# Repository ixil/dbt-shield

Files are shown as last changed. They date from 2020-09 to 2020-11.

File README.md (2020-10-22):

# dbt-shield
Shield: Pellet extrusion controller for ABB robotic arms w/ profinet I/O

Mini-shield: Filament extrusion controller for UR arms, to be used in the MAS ETH DFAB

## Shield
---
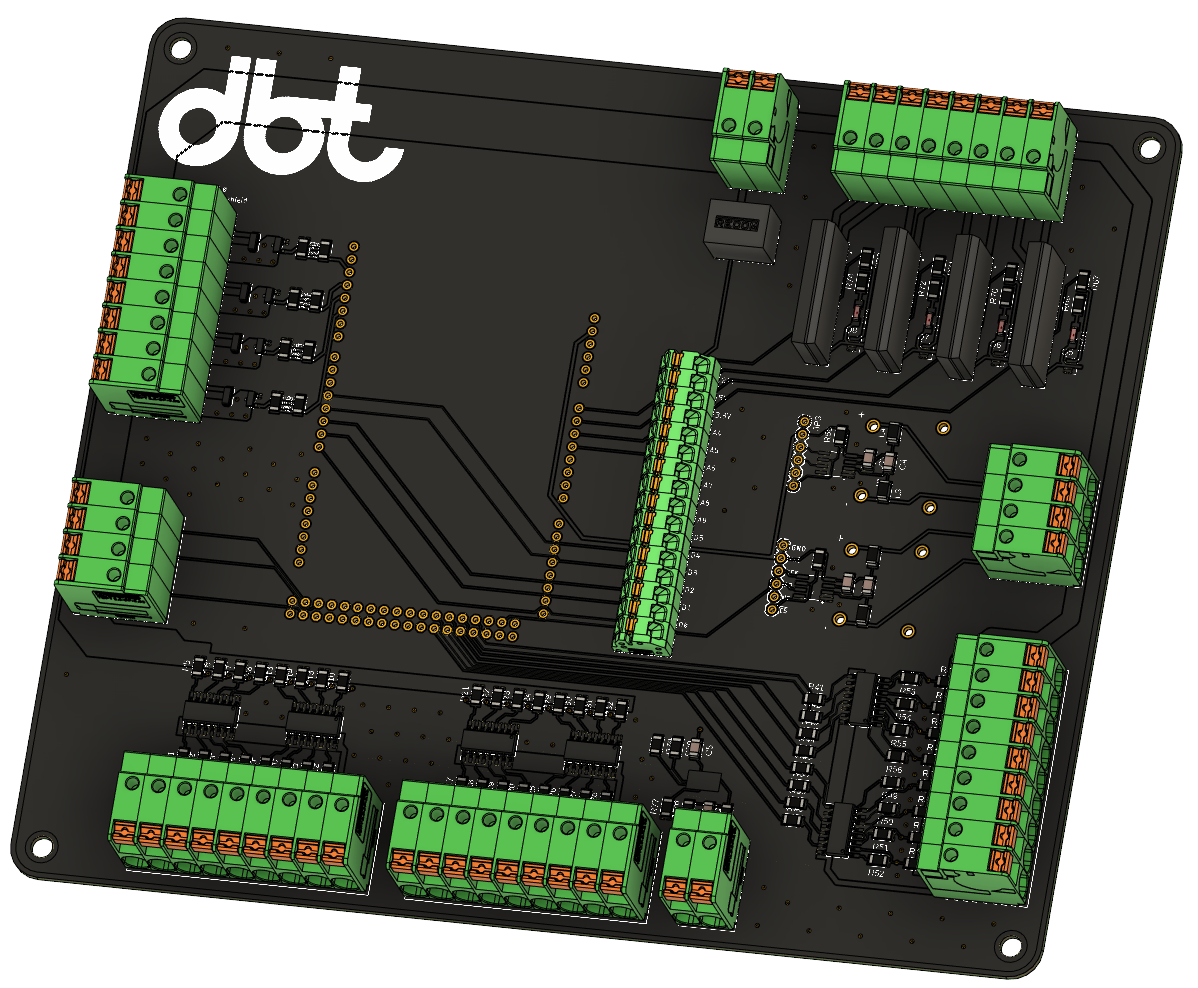
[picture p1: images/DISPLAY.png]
d


### Specs
---
16bit 24V digital Input\
8bit 24v digital Output\
4bit 0-10v analog Input\
4x 500mW MOSFETS\
4x SSR 240VAC 2A\
2x K-Type Thermocouple amplifiers

## Mini-Shield
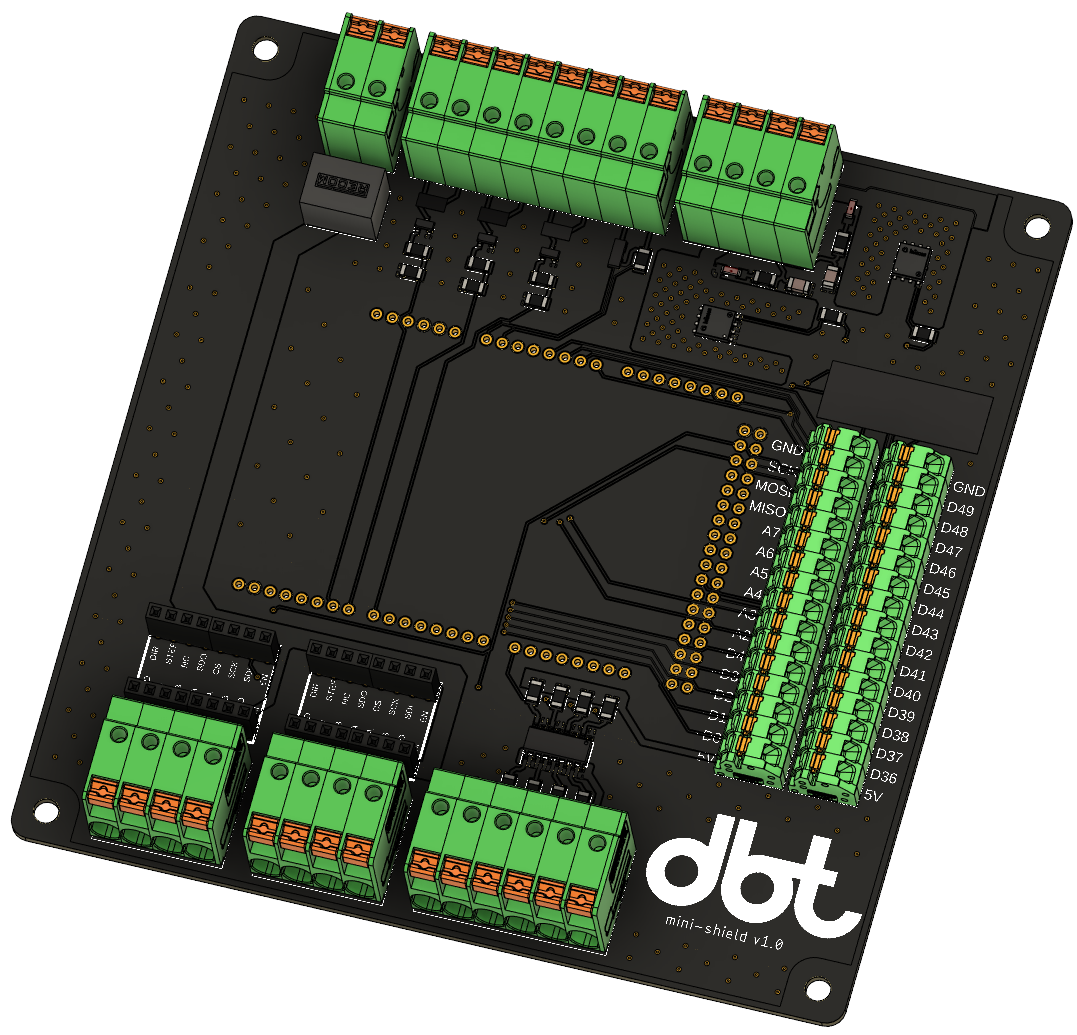
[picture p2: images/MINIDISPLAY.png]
minid


### Specs
---
4bit 24V digital Input\
2x TMC2130 Stepper Driver\
2x 100W MOSFETS\
3x 500mW MOSFETS\
1x 104NT thermistor

[Pin-Out / Set-Up / Connections](https://github.com/hiiragii/dbt-shield/tree/master/mini)

### UR5 FDM  

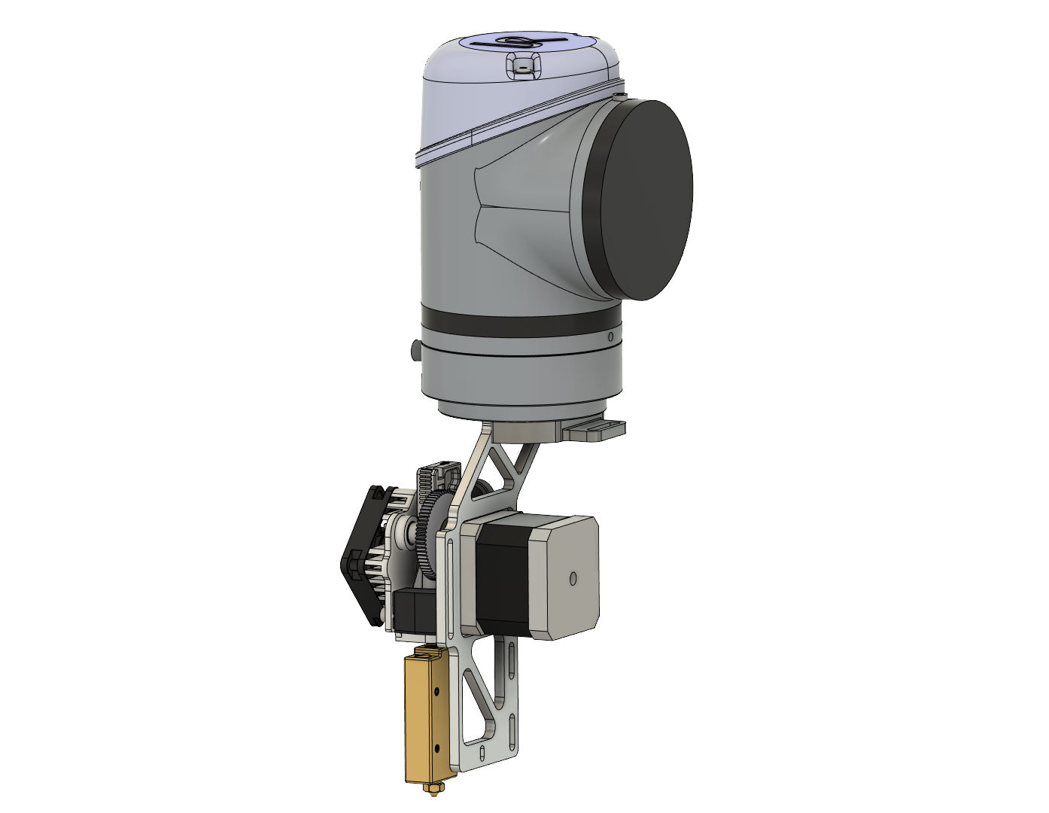
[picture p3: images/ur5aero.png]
ur5


UR 5 e3d Titan Aero + Super Volcano mounting bracket
[stl / step files](https://github.com/hiiragii/dbt-shield/tree/master/ur5aero)

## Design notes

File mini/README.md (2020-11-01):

## Pinout
---
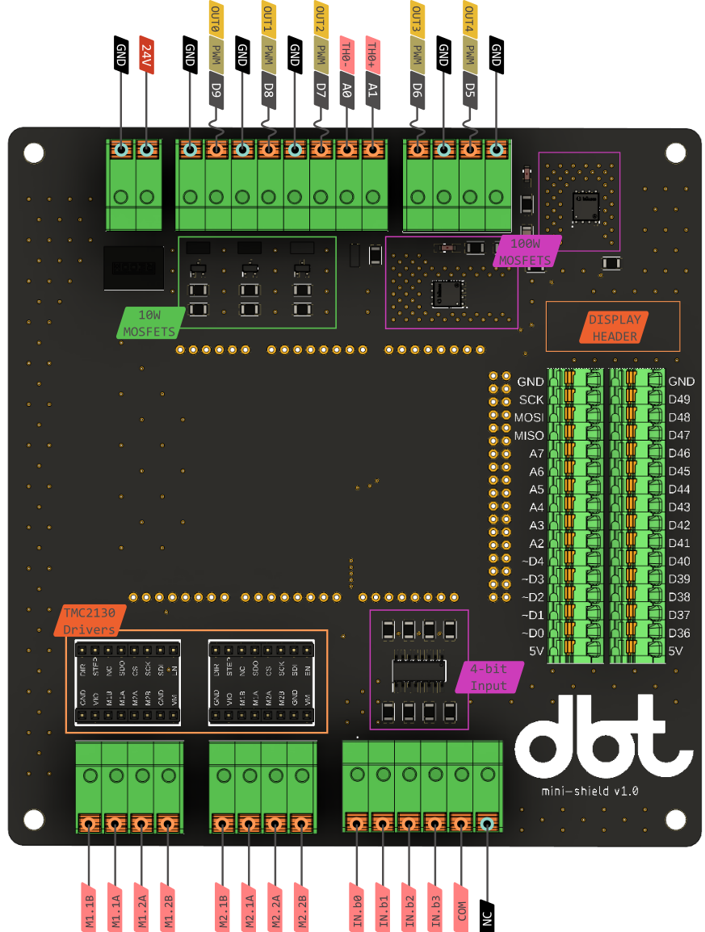
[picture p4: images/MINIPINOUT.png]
pinout

The 2x16 pin terminal blocks on the right side are directly connected to the respective arduino pin (eg D0 on the terminal block is digital pin 0 on the arduino).

## Connections
---
+ Connect the 24v power supply wires to the top terminal.
+ Connect the Extruder optional object fan to OUT0 and OUT1.
+ Connect the thermistor leads to TH0+ and TH0-, polarity doesn't matter.
+ Connect the super-volcano heater to OUT3 and GND (first 2 pins on the terminal block).
+ Connect the first stepper coil to M1.1A and M1.1B. Connect the second coil to M1.2A and M1.2B. Polarity doesn't matter, you can reverse the direction of rotation directly in software or by swapping 2 leads of the same coil (eg. M1.1A and M1.1B).  
+ Connect the 5 lead cable to the 4-bit input terminal block, where IN.b3 is the MSB.

## Set-up
---

## Digital-Input

In.b0 = heater enable, active LOW
In.b1 = stepper enable, active LOW
In.b2 = speed 
In.b3 = speed 

speed(5mm/s)  01
speed(15mm/s) 10
speed(30mm/s) 11

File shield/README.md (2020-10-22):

## Pinout
---
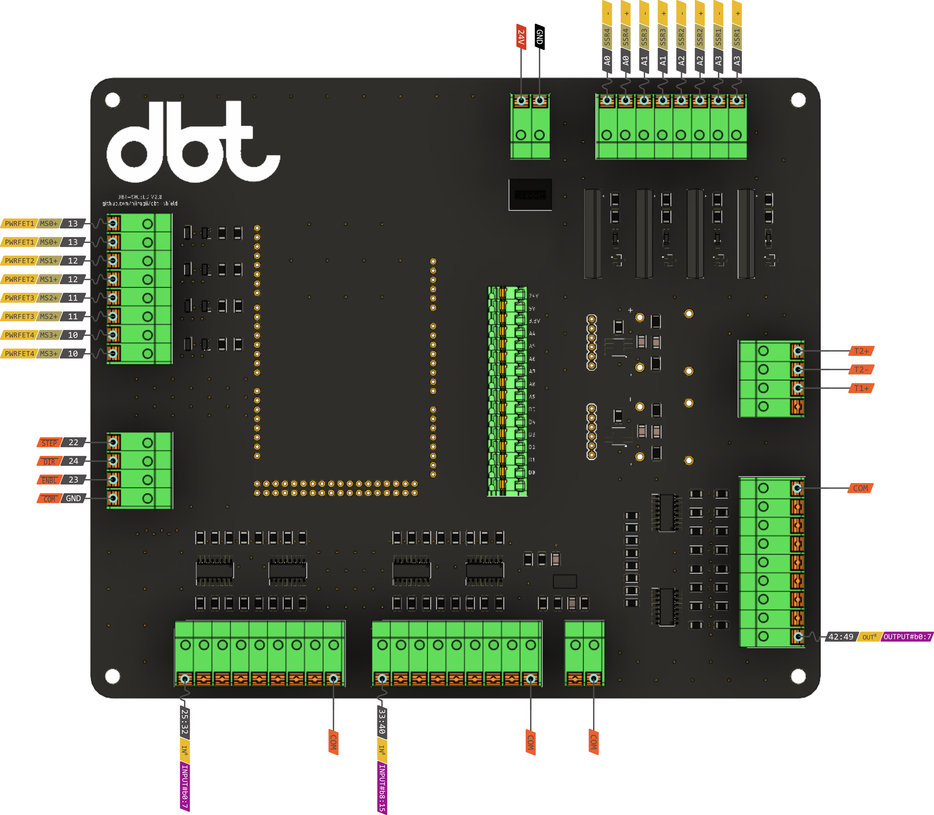
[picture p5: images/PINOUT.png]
pinout


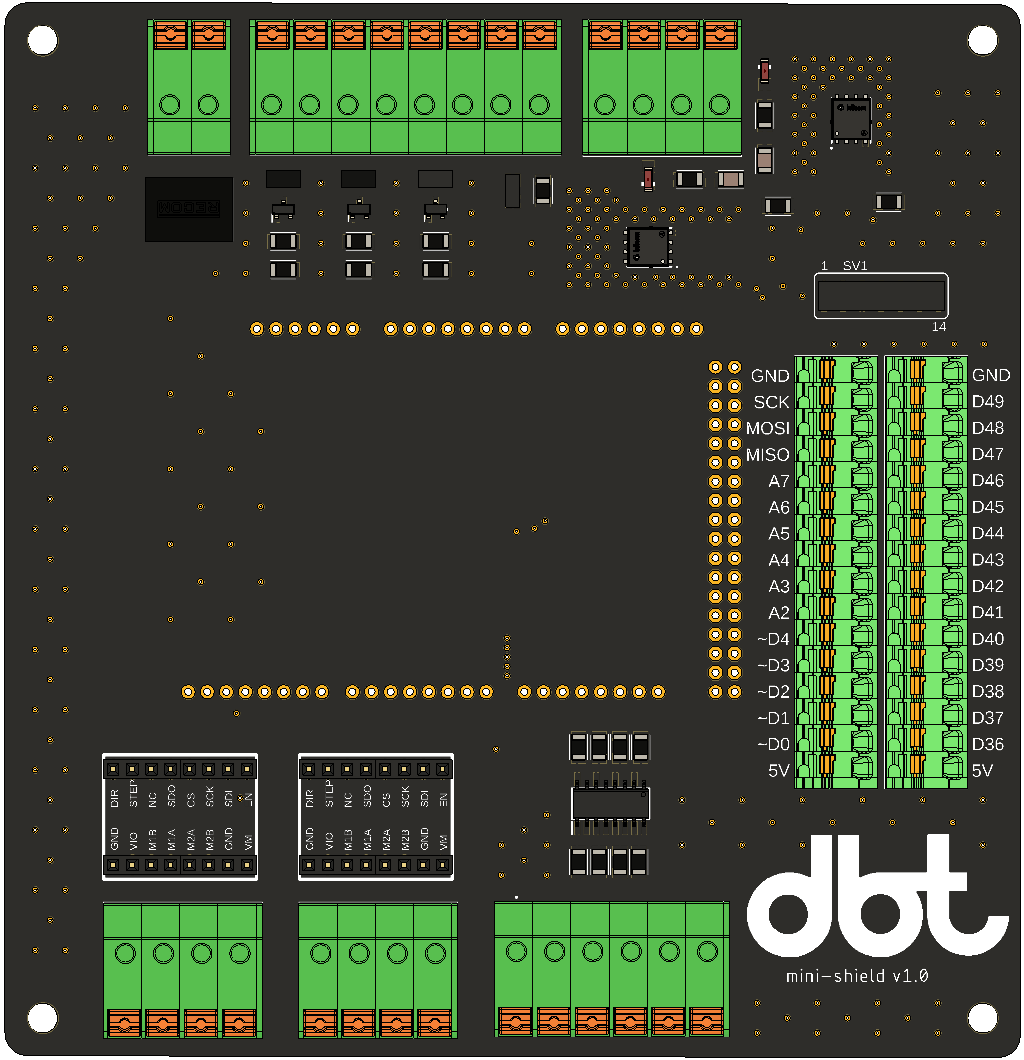
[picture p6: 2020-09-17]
images/MINIFRONT.png

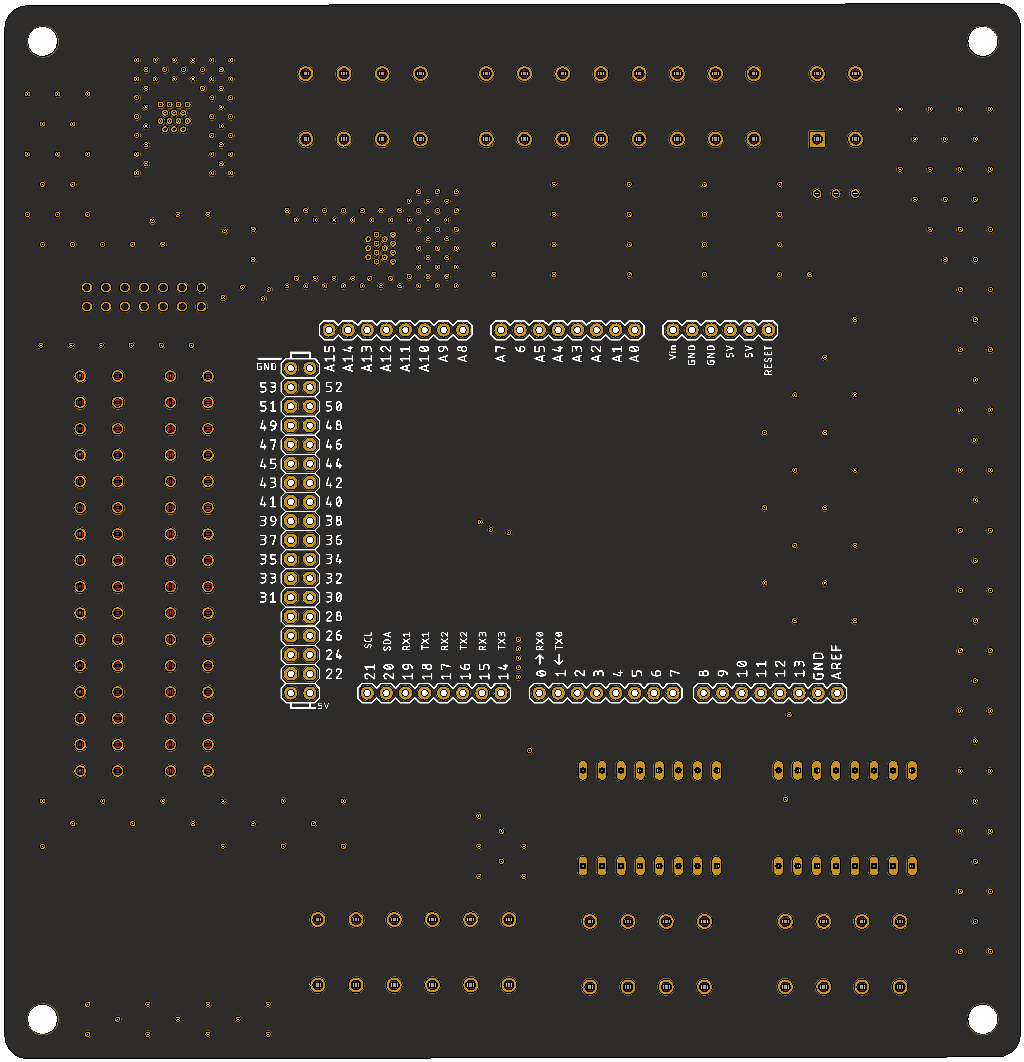
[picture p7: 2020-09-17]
images/MINIBACK.png

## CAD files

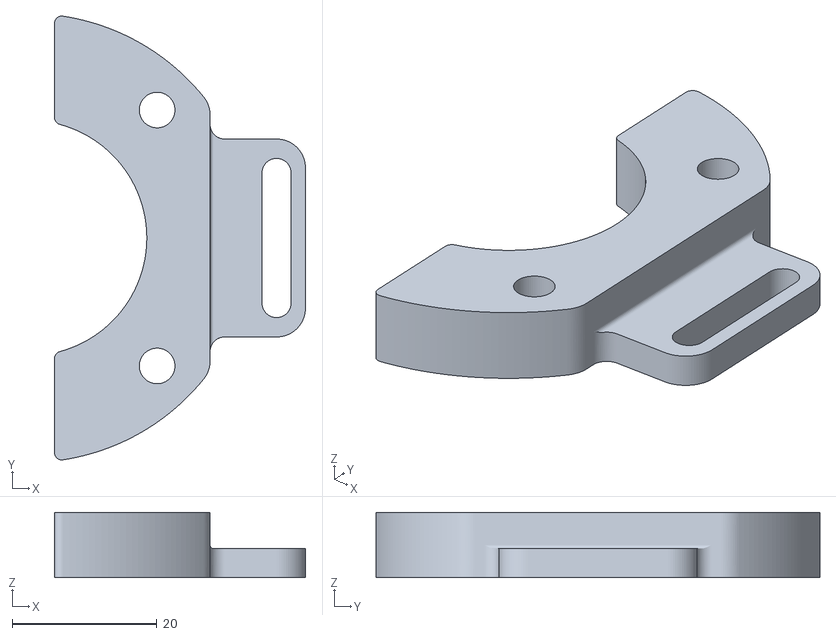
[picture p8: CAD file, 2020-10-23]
ur5aero/dbt-aero-bracket1.stl
34.7 x 61.3 x 9.00

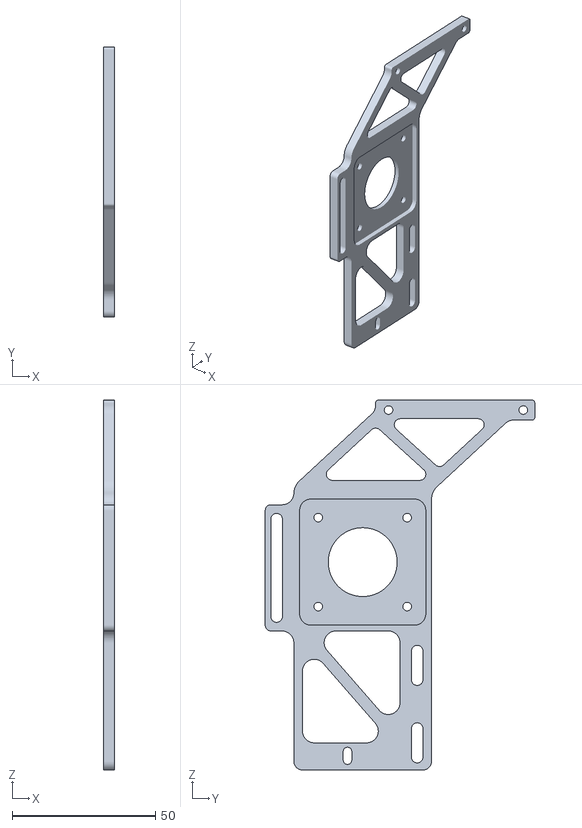
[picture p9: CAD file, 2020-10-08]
ur5aero/dbt_ur5_aero_bracket1.stl
4.00 x 94.0 x 129.0

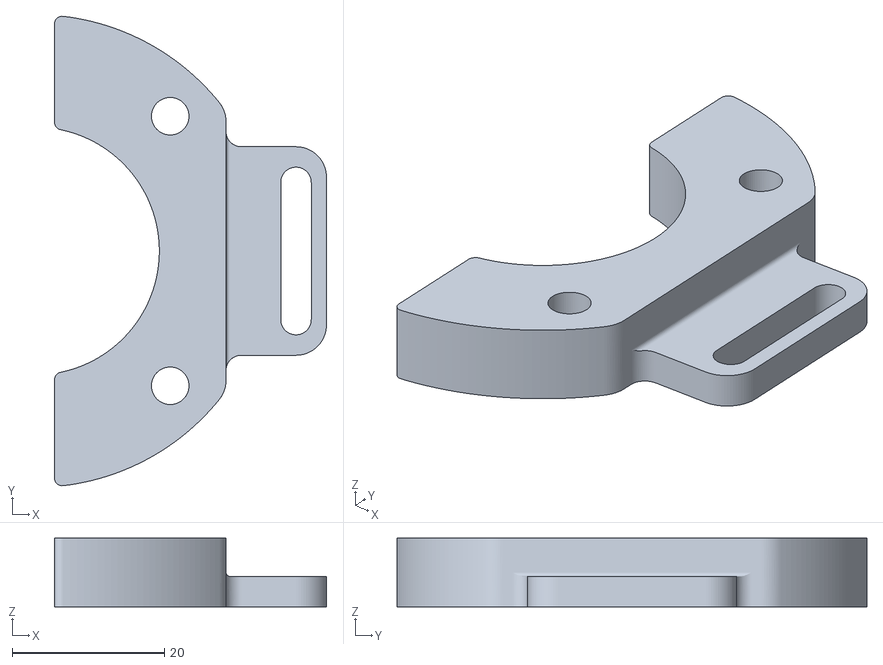
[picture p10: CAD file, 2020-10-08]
ur5aero/dbt_ur5_aero_bracket2.stl
35.7 x 61.6 x 9.00

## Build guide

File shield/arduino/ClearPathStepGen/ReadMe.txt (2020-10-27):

This Library sends pulsed step and Direction signals to ClearPath motors to precisly control position, and velocity of up to 6 motors simulateously up to 4000RPM.  The methodology used to create the pulse step and direction signals is not compatible with stepper motors, or with other servo systems.  The pulsed step and direction also requires a RAS setting of at least 16 ms on all ClearPath motors, a longer RAS will results in quieter motion.

This library defines two classes used to manage and control the motors:ClearPathMotorSD, and ClearPathStepGen.

The ClearPathMotorSD class is used to manage an individual motor including setting up pins, commanding moves, setting velocity/acceleration etc.  The following is a list of commands in this class:

--- ClearPathMotorSD - default constructor for initializing the motor

--- attach() - Attachs pins to this motor, and declares them as input/outputs

--- stopMove()  - Interupts the current move, the motor may abruptly stop

--- move() - sets the maximum veloctiy

--- moveWithVelocity() - moves continuously at a velocity

--- disable() - disables the motor

--- enable() - enables the motor

--- getCommandedPosition() - Returns the absolute cmomanded position where the position on enable=0

--- readHLFB() - Returns the value of the motor's HLFB Pin

--- setMaxVel() - sets the maximum veloctiy

--- setMaxAccel() - sets the acceleration

--- commandDone() - returns wheter or not there is a valid current command

The ClearPathStepGen class is the class which manages the sending of the pulsed step and direction signals to all motors.  This is accomplished by setting up a Timer based ISR at around 2kHz (using Timer2), and directly writing to the I/O register Port B.  Becuase only PORTB is used to send step signals, the B input of the ClearPath motors must be connected to pins 8-13 on an Arduino Uno.  Unused pins on PORTB may be used for other function without interfereing with this library.

NOTE: If you are using another type of arduino besides the UNO, the ClearPathStepGen must be modified to output on a different PORT and/or the Contrustor function must be modified to correctly relate the pin numbers to the bits of the I/O Resister you would like to use.  For example,

In an Arduino Mega, PORTA refers to pins, 22-29, so to modify this library to use a Mega simply:

1) Do a find/replace all replacing "PORTB" with "PORTA"  (case sensitive, ignore quotes).

2) Do a find/replace all replacing "->PinB-8" with "->PinB-22" (case sensitive, ignore quotes).

After this, you could use an Arduino Mega and connect input B to pins 22-29

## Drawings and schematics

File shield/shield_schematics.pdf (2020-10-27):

# ARDUINO / CONNS

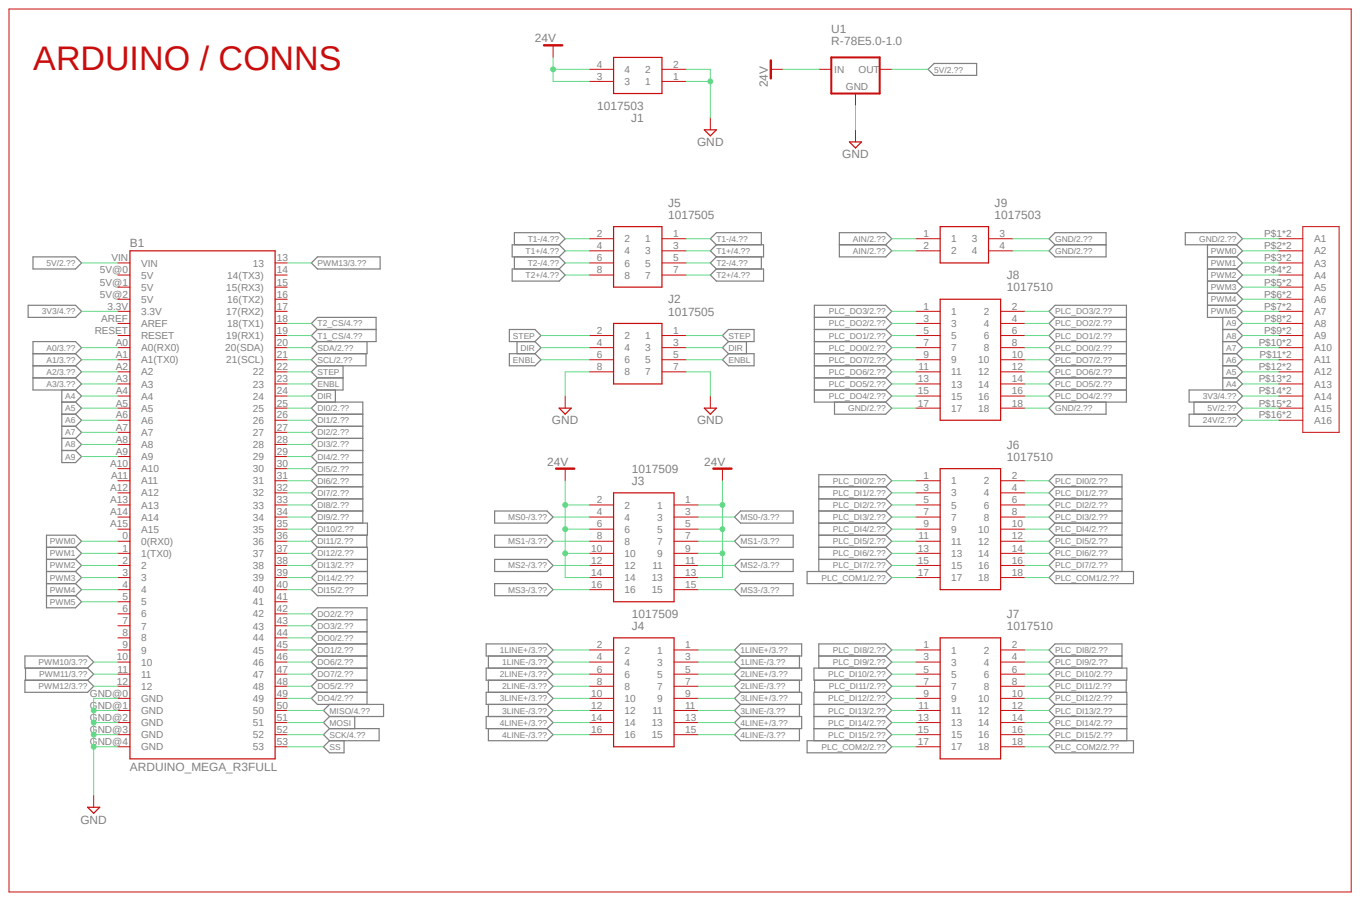
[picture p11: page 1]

MISO/4.?? MOSI SCK/4.?? SS

16-bit Input | 8-bit Output

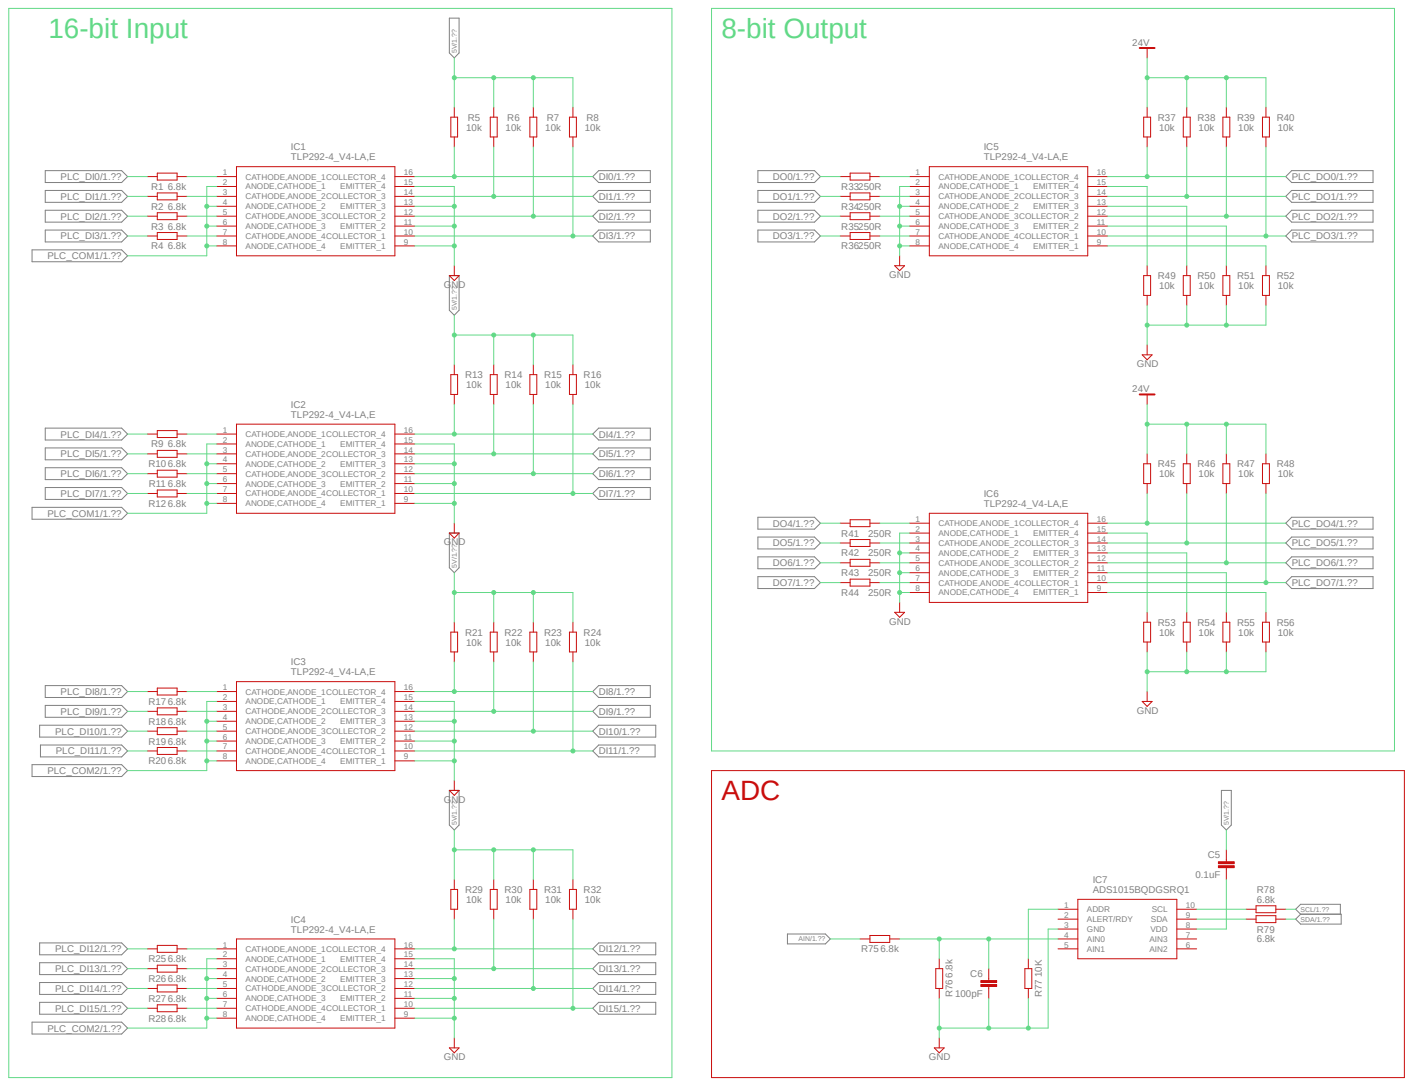
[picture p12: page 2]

24V 10k

24V 10k

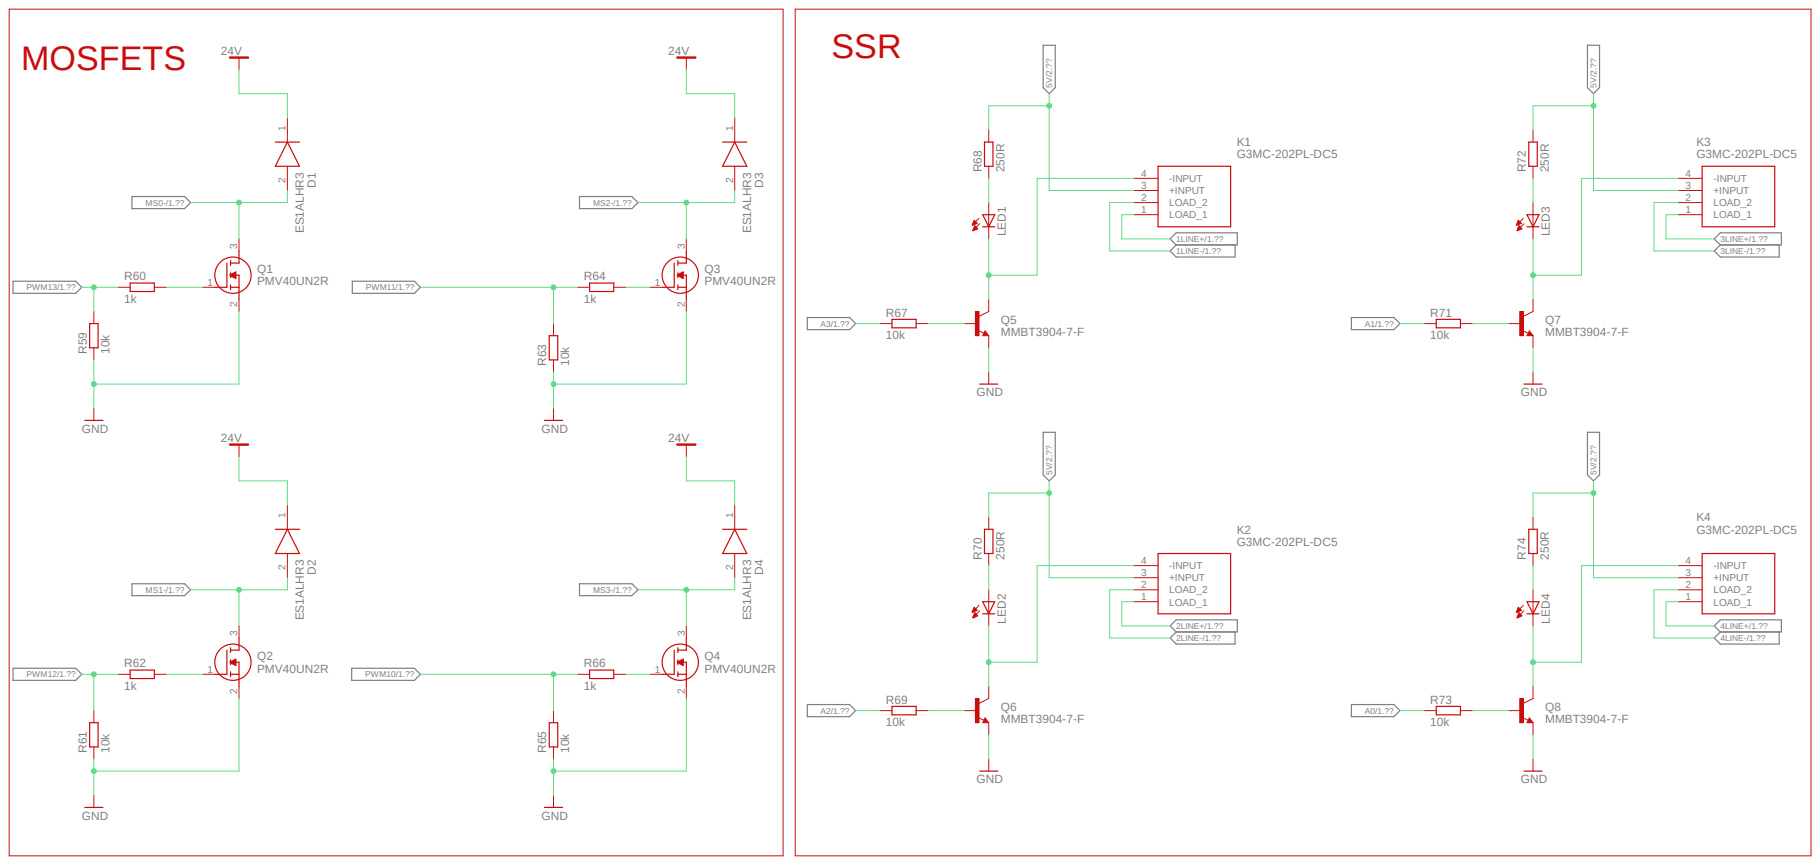
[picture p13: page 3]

# MAX31855K

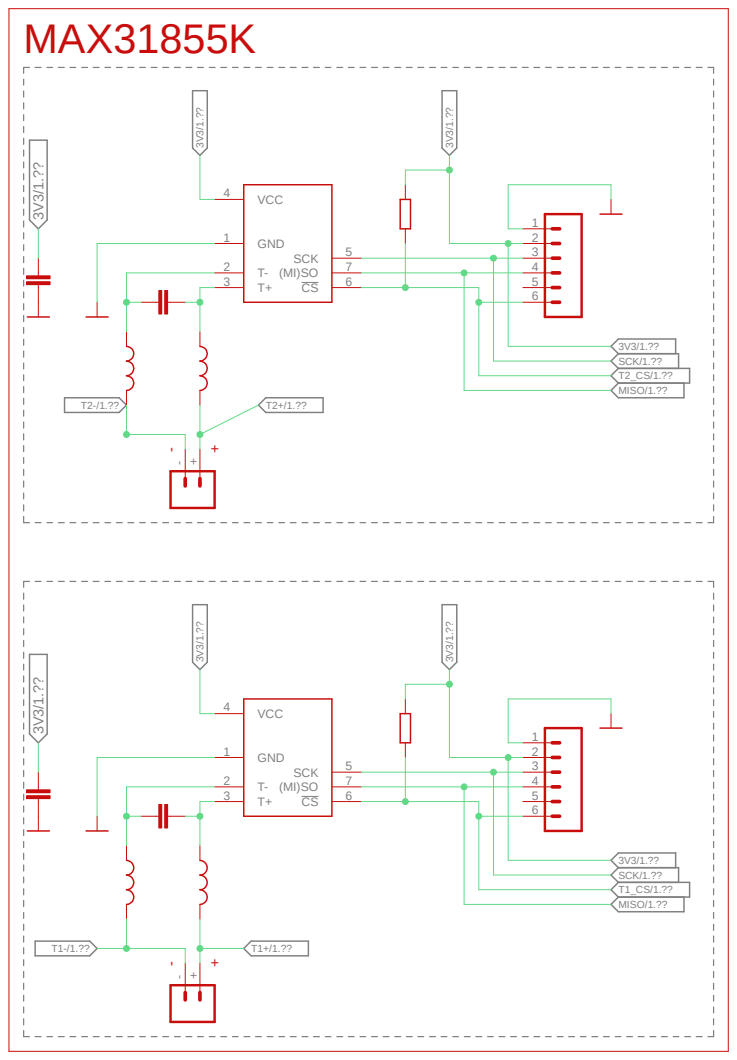
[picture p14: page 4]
GND 1; VCC 4; 6 SCK; -+ GND 1 T- 2 T+ 3 VCC 4; SCK/1.??; T1+/1.?? ³V³/1.??; 3V3/1.?? ³V³/1.??; MISO/1.??; MISO/1.?? T2-/1.??

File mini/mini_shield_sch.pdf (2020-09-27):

# DBT MINI-SHIELD https://github.com/hiiragii/dbt-shield/mini

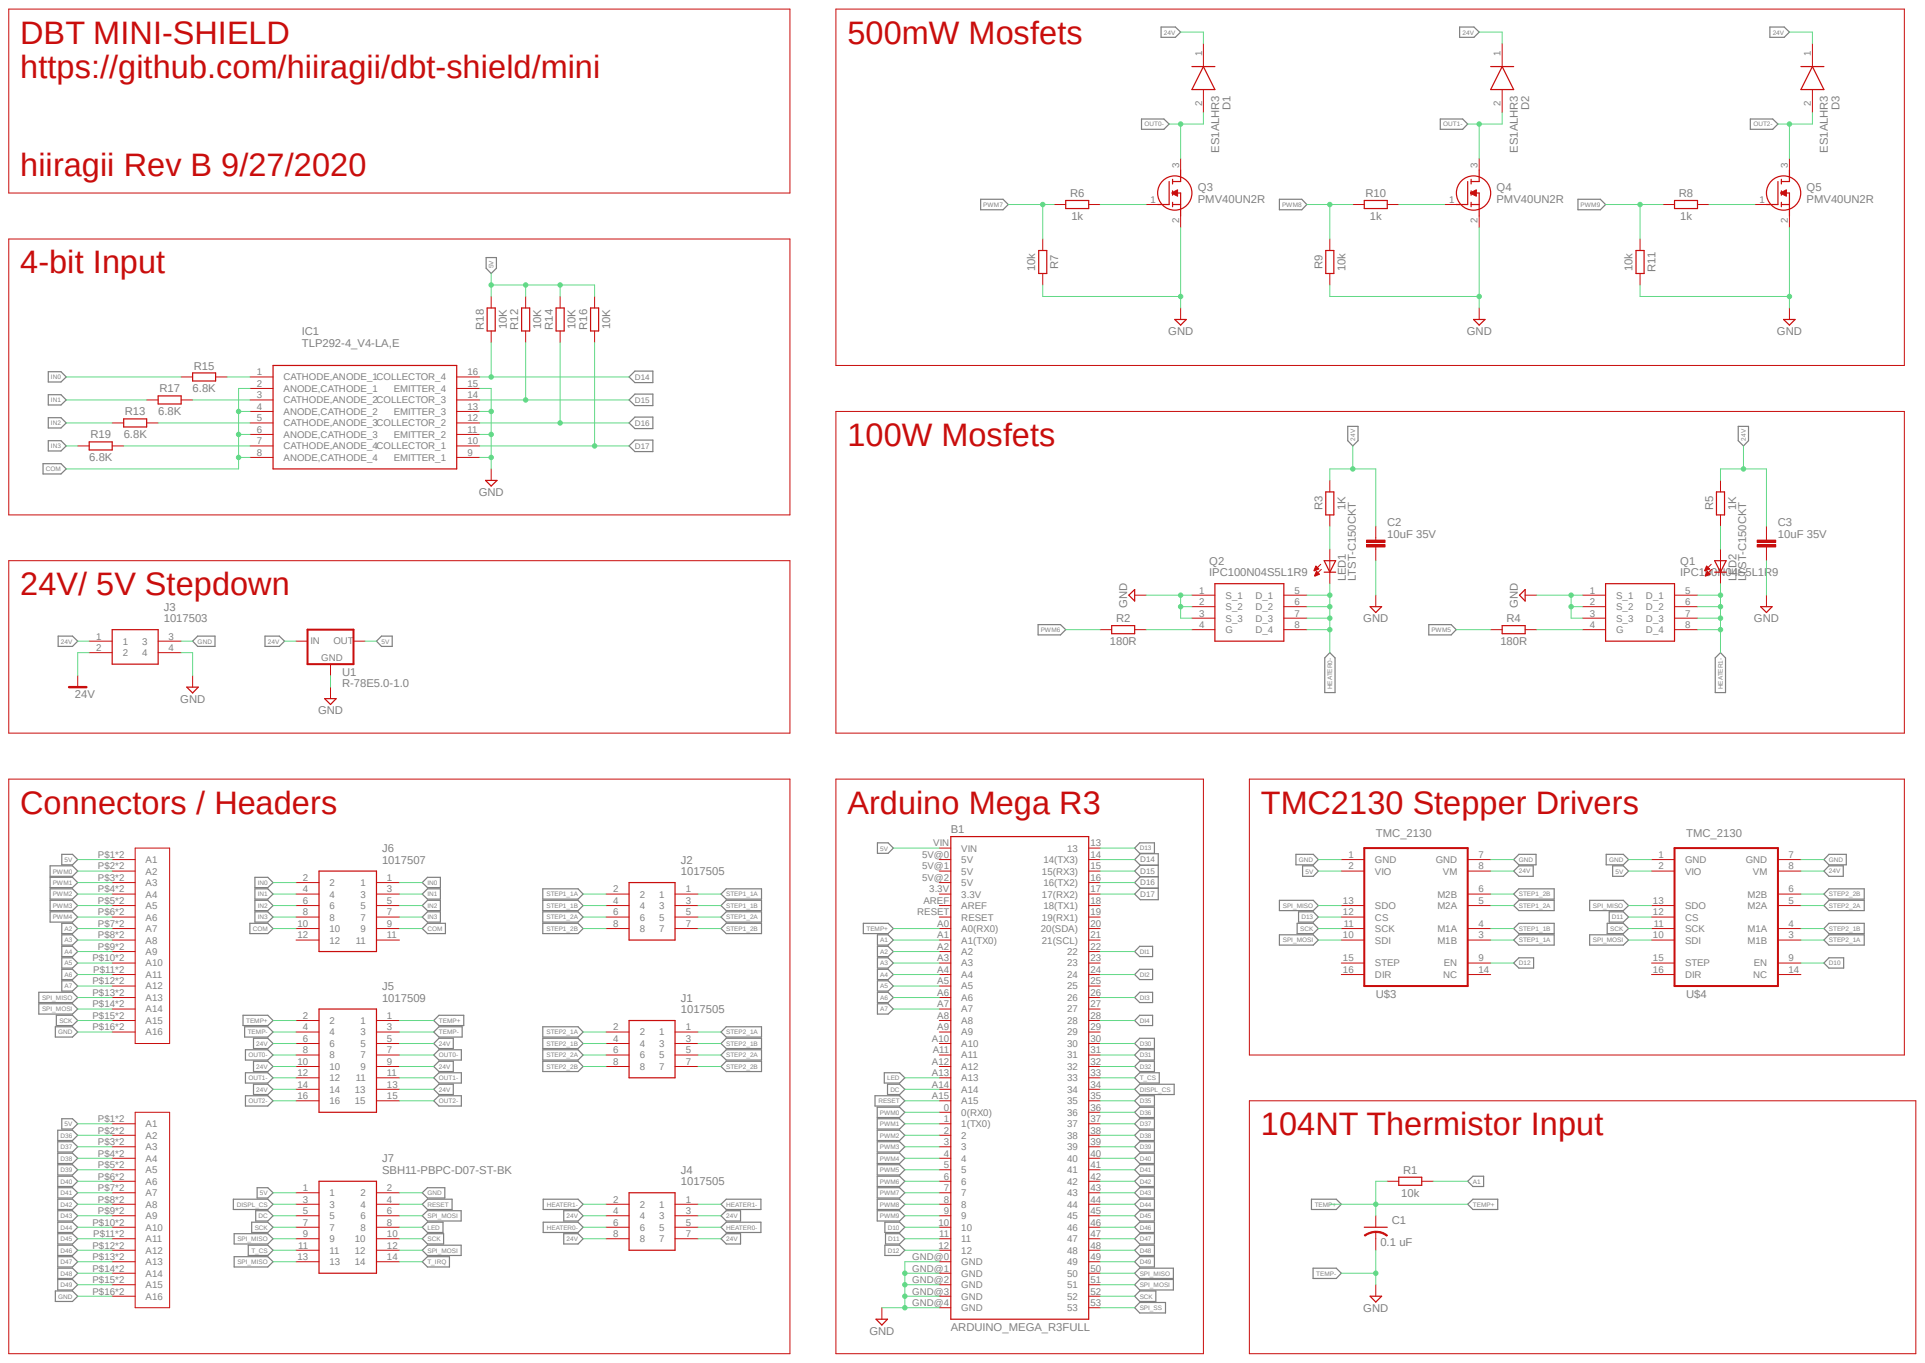
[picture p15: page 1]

PWM1 | D37
PWM2 | D38
PWM3 | D39
PWM4 | D40
PWM5 | D41
PWM6 | D42

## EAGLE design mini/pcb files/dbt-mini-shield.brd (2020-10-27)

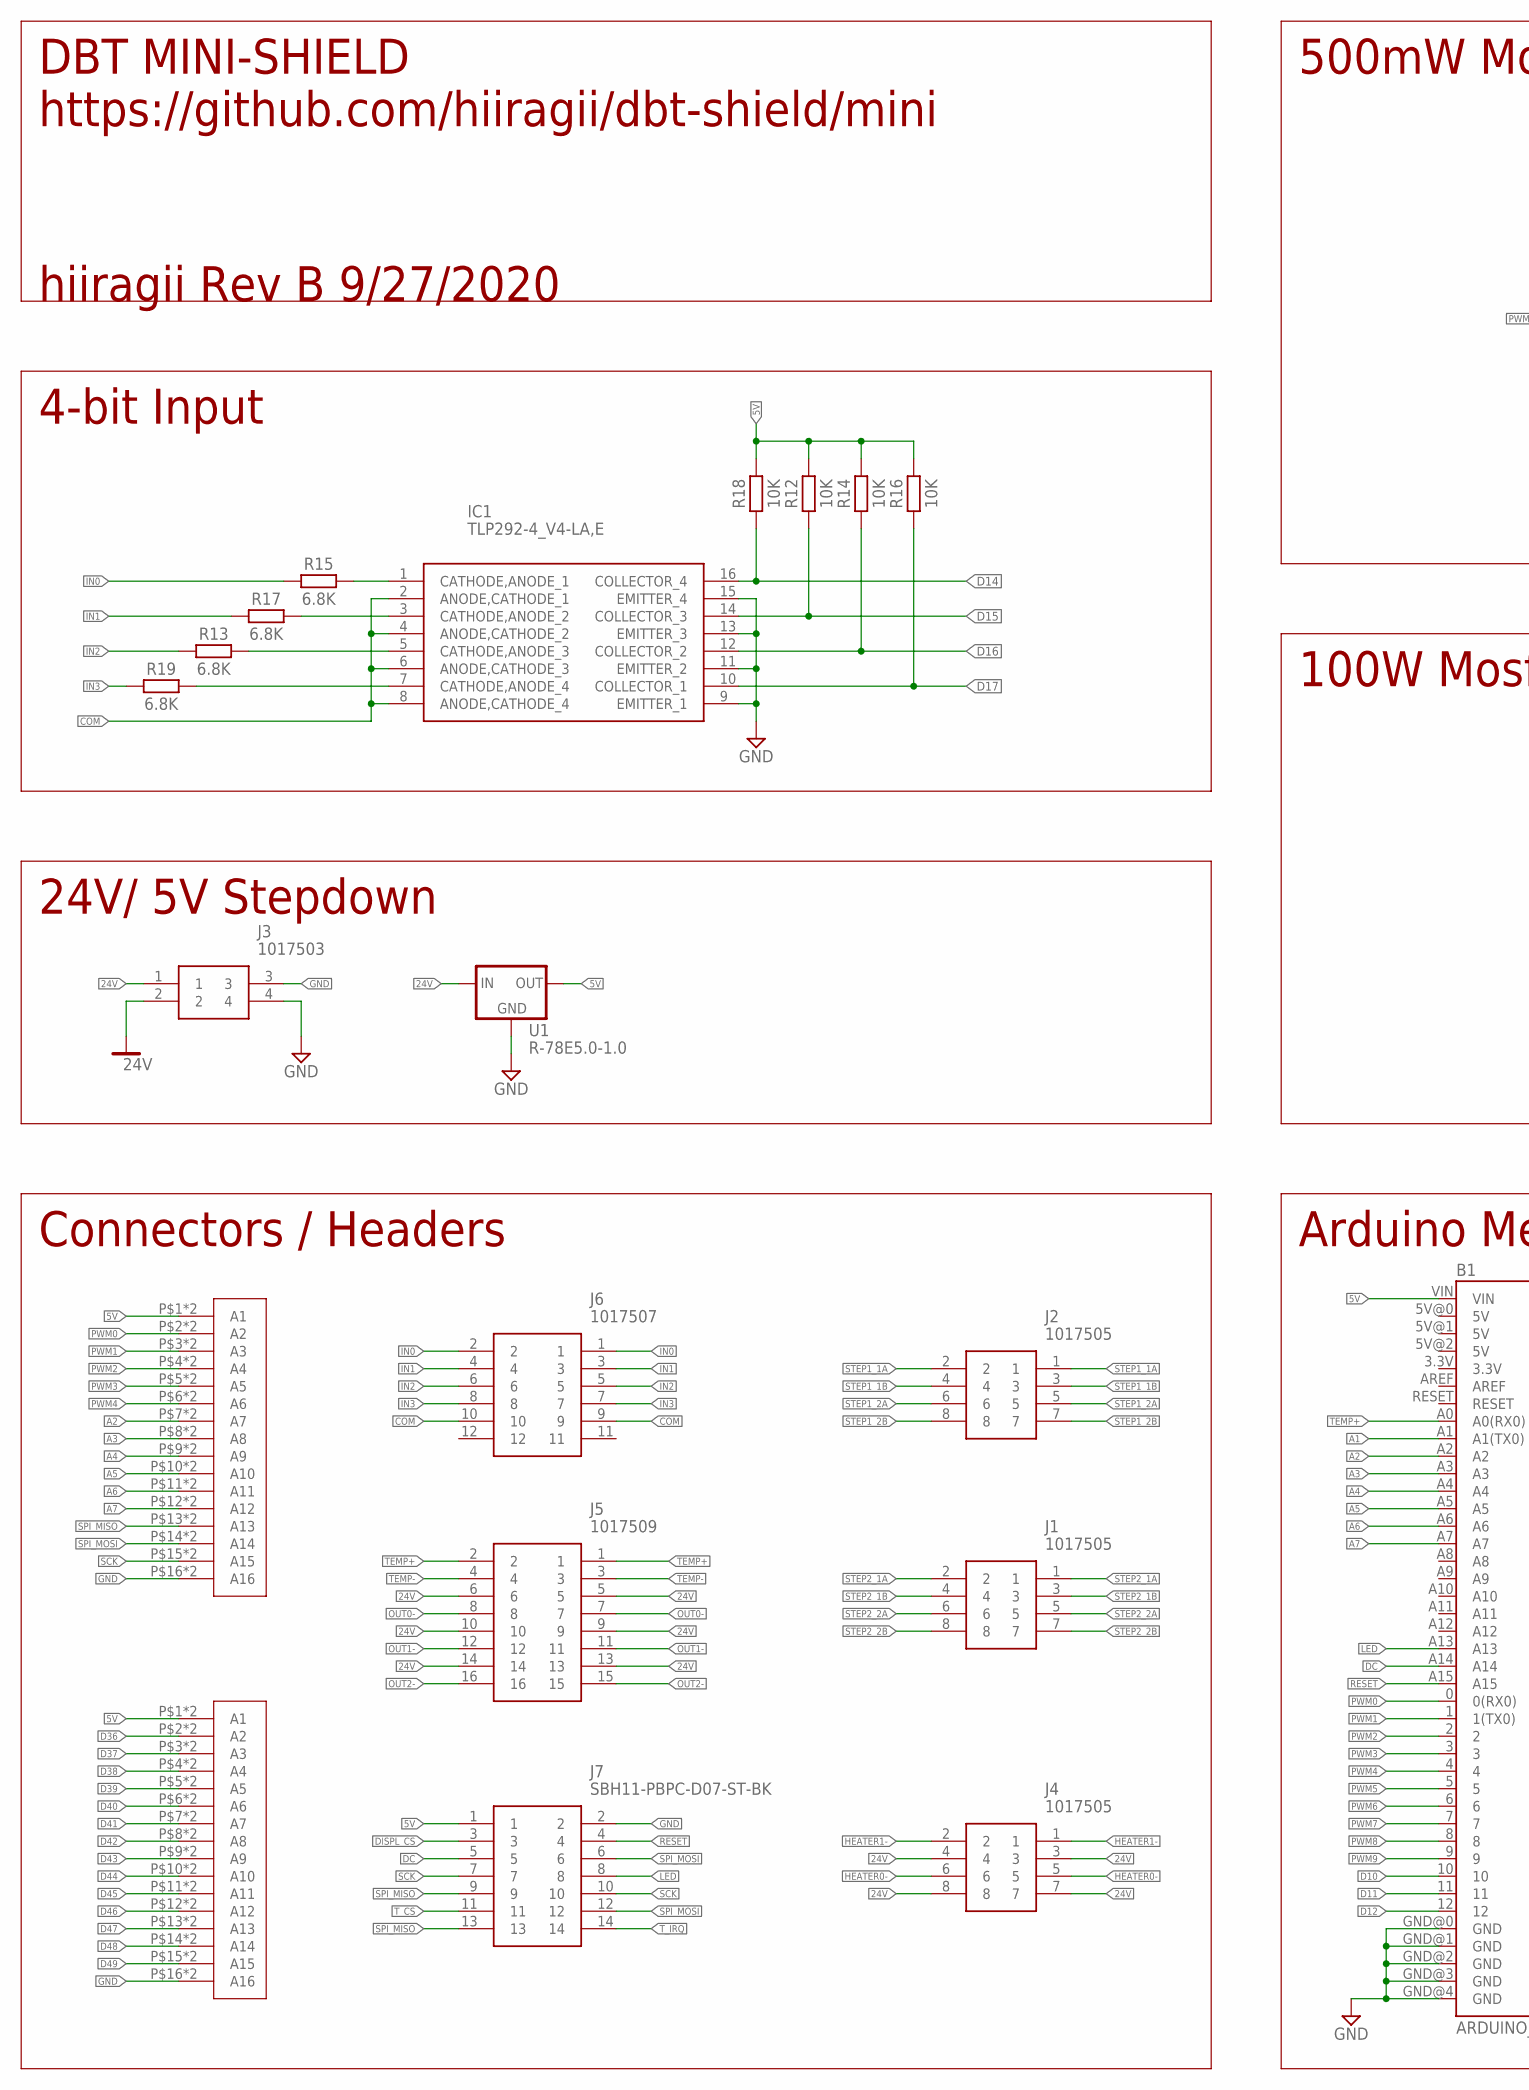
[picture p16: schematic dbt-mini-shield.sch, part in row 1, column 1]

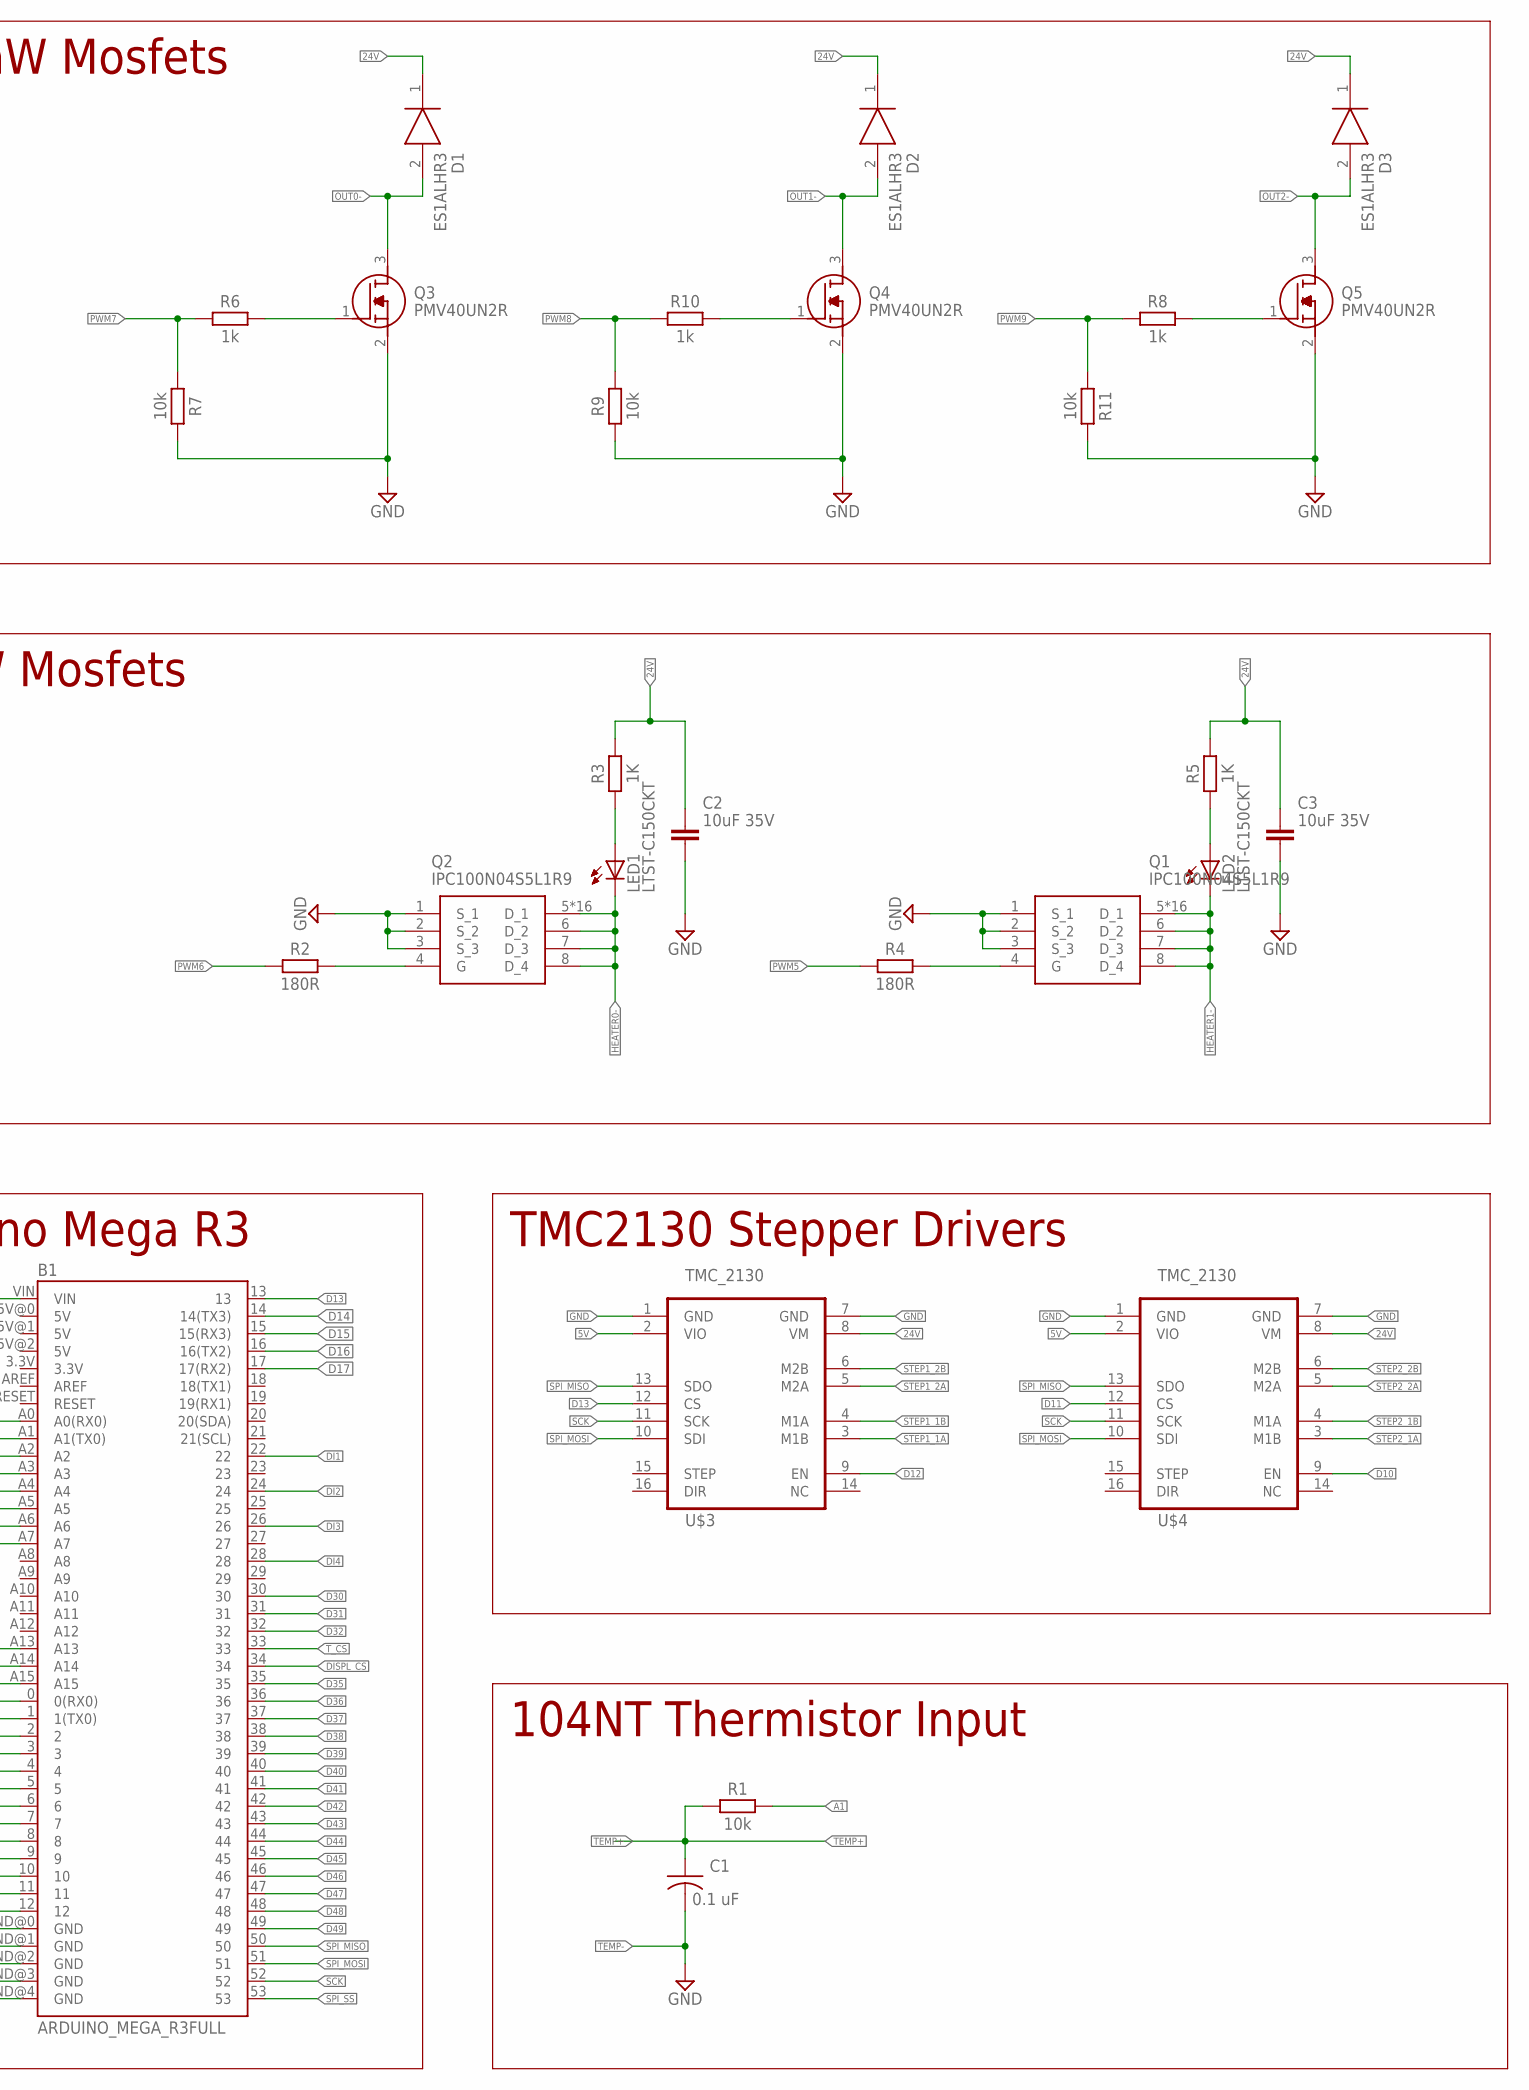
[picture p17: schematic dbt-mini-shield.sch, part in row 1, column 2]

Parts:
B1: ARDUINO_MEGA_R3FULL; ARDUINO_MEGA
C1: 0.1 uF; C1206
C2, C3: 10uF 35V; CAPC3216X135
D1, D2, D3: ES1ALHR3; SODFL3618X143N
IC1: TLP292-4_V4-LA,E; SOIC127P700X230-16N
J1, J2, J4: 1017505
J3: 1017503
J5: 1017509
J6: 1017507
J7: SBH11-PBPC-D07-ST-BK; SHDR14W64P254_2X7_2528X910X910
LED1, LED2: LTST-C150CKT; CHIPLED_1206
Q1, Q2: IPC100N04S5L1R9; PG-TDSON-8
Q3, Q4, Q5: PMV40UN2R; SOT95P230X110-3N
R1, R7, R9, R11: 10k; RESC3216X70
R2, R4: 180R; RESC3216X70
R3, R5: 1K; RESC3216X70
R6, R8, R10: 1k; RESC3216X70
R12, R14, R16, R18: 10K; RESC3216X70
R13, R15, R17, R19: 6.8K; RESC3216X70
U1: R-78E5.0-1.0; DC-DC_CONVERTER_78XX
U$1, U$2: 1861991
U$3, U$4: TMC_2130

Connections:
5V: B1.VIN, J7.1, R12.2, R14.2, R16.2, R18.2, U1.VOUT (OUT), U$1.P$1 (A1), U$1.P$17 (A1), U$2.P$1 (A1), U$2.P$17 (A1), U$3.2 (VIO), U$4.2 (VIO)
24V: C2.1, C3.1, D1.1 (K), D2.1 (K), D3.1 (K), J3.1, J3.2, J4.3, J4.4, J4.7, J4.8, J5.5, J5.6, J5.9, J5.10, J5.13, J5.14, R3.2, R5.2, U1.VIN (IN), U$3.8 (VM), U$4.8 (VM)
A1: B1.A1 (A1(TX0)), R1.2
A2: B1.A2, U$1.P$7 (A7), U$1.P$23 (A7)
A3: B1.A3, U$1.P$8 (A8), U$1.P$24 (A8)
A4: B1.A4, U$1.P$9 (A9), U$1.P$25 (A9)
A5: B1.A5, U$1.P$10 (A10), U$1.P$26 (A10)
A6: B1.A6, U$1.P$11 (A11), U$1.P$27 (A11)
A7: B1.A7, U$1.P$12 (A12), U$1.P$28 (A12)
COM: IC1.2 (ANODE,CATHODE_1), IC1.4 (ANODE,CATHODE_2), IC1.6 (ANODE,CATHODE_3), IC1.8 (ANODE,CATHODE_4), J6.9, J6.10
D10: B1.10, U$4.9 (EN)
D11: B1.11, U$4.12 (CS)
D12: B1.12, U$3.9 (EN)
D13: B1.13, U$3.12 (CS)
D14: B1.14 (14(TX3)), IC1.16 (COLLECTOR_4), R18.1
D15: B1.15 (15(RX3)), IC1.14 (COLLECTOR_3), R12.1
D16: B1.16 (16(TX2)), IC1.12 (COLLECTOR_2), R14.1
D17: B1.17 (17(RX2)), IC1.10 (COLLECTOR_1), R16.1
D30: B1.30
D31: B1.31
D32: B1.32
D35: B1.35
D36: B1.36, U$2.P$2 (A2), U$2.P$18 (A2)
D37: B1.37, U$2.P$3 (A3), U$2.P$19 (A3)
D38: B1.38, U$2.P$4 (A4), U$2.P$20 (A4)
D39: B1.39, U$2.P$5 (A5), U$2.P$21 (A5)
D40: B1.40, U$2.P$6 (A6), U$2.P$22 (A6)
D41: B1.41, U$2.P$7 (A7), U$2.P$23 (A7)
D42: B1.42, U$2.P$8 (A8), U$2.P$24 (A8)
D43: B1.43, U$2.P$9 (A9), U$2.P$25 (A9)
D44: B1.44, U$2.P$10 (A10), U$2.P$26 (A10)
D45: B1.45, U$2.P$11 (A11), U$2.P$27 (A11)
D46: B1.46, U$2.P$12 (A12), U$2.P$28 (A12)
D47: B1.47, U$2.P$13 (A13), U$2.P$29 (A13)
D48: B1.48, U$2.P$14 (A14), U$2.P$30 (A14)
D49: B1.49, U$2.P$15 (A15), U$2.P$31 (A15)
DC: B1.A14, J7.5
DI1: B1.22
DI2: B1.24
DI3: B1.26
DI4: B1.28
DISPL_CS: B1.34, J7.3
G: Q2.4 (G), R2.2
G1: Q1.4 (G), R4.2
GND: B1.GND@0 (GND), B1.GND@1 (GND), B1.GND@2 (GND), B1.GND@3 (GND), B1.GND@4 (GND), C2.2, C3.2, IC1.9 (EMITTER_1), IC1.11 (EMITTER_2), IC1.13 (EMITTER_3), IC1.15 (EMITTER_4), J3.3, J3.4, J7.2, Q1.1 (S_1), Q1.2 (S_2), Q1.3 (S_3), Q2.1 (S_1), Q2.2 (S_2), Q2.3 (S_3), Q3.2 (S), Q4.2 (S), Q5.2 (S), R7.2, R9.1, R11.2, U1.GND, U$1.P$16 (A16), U$1.P$32 (A16), U$2.P$16 (A16), U$2.P$32 (A16), U$3.1 (GND), U$3.7 (GND), U$4.1 (GND), U$4.7 (GND)
HEATER0-: J4.5, J4.6, LED1.C, Q2.5 (D_1), Q2.6 (D_2), Q2.7 (D_3), Q2.8 (D_4), Q2.9 (D_1), Q2.P$1 (D_1), Q2.P$2 (D_1), Q2.P$3 (D_1), Q2.P$4 (D_1), Q2.P$5 (D_1), Q2.P$6 (D_1), Q2.P$7 (D_1), Q2.P$8 (D_1), Q2.P$9 (D_1), Q2.P$10 (D_1), Q2.P$11 (D_1), Q2.P$12 (D_1), Q2.P$13 (D_1), Q2.P$14 (D_1)
HEATER1-: J4.1, J4.2, LED2.C, Q1.5 (D_1), Q1.6 (D_2), Q1.7 (D_3), Q1.8 (D_4), Q1.9 (D_1), Q1.P$1 (D_1), Q1.P$2 (D_1), Q1.P$3 (D_1), Q1.P$4 (D_1), Q1.P$5 (D_1), Q1.P$6 (D_1), Q1.P$7 (D_1), Q1.P$8 (D_1), Q1.P$9 (D_1), Q1.P$10 (D_1), Q1.P$11 (D_1), Q1.P$12 (D_1), Q1.P$13 (D_1), Q1.P$14 (D_1)
IN0: J6.1, J6.2, R15.1
IN1: J6.3, J6.4, R17.1
IN2: J6.5, J6.6, R13.1
IN3: J6.7, J6.8, R19.1
LED: B1.A13, J7.8
unnamed: LED1.A, R3.1
unnamed: LED2.A, R5.1
unnamed: IC1.1 (CATHODE,ANODE_1), R15.2
unnamed: IC1.3 (CATHODE,ANODE_2), R17.2
unnamed: IC1.5 (CATHODE,ANODE_3), R13.2
unnamed: IC1.7 (CATHODE,ANODE_4), R19.2
unnamed: Q3.1 (G), R6.2
unnamed: Q4.1 (G), R10.2
unnamed: Q5.1 (G), R8.2
NC: U$3.14 (NC), U$4.14 (NC)
OUT0-: D1.2 (A), J5.7, J5.8, Q3.3 (D)
OUT1-: D2.2 (A), J5.11, J5.12, Q4.3 (D)
OUT2-: D3.2 (A), J5.15, J5.16, Q5.3 (D)
PWM0: B1.0 (0(RX0)), U$1.P$2 (A2), U$1.P$18 (A2)
PWM1: B1.1 (1(TX0)), U$1.P$3 (A3), U$1.P$19 (A3)
PWM2: B1.2, U$1.P$4 (A4), U$1.P$20 (A4)
PWM3: B1.3, U$1.P$5 (A5), U$1.P$21 (A5)
PWM4: B1.4, U$1.P$6 (A6), U$1.P$22 (A6)
PWM5: B1.5, R4.1
PWM6: B1.6, R2.1
PWM7: B1.7, R6.1, R7.1
PWM8: B1.8, R9.2, R10.1
PWM9: B1.9, R8.1, R11.1
RESET: B1.A15, J7.4
SCK: B1.52, J7.7, J7.10, U$1.P$15 (A15), U$1.P$31 (A15), U$3.11 (SCK), U$4.11 (SCK)
SPI_MISO: B1.50, J7.9, J7.13, U$1.P$13 (A13), U$1.P$29 (A13), U$3.13 (SDO), U$4.13 (SDO)
SPI_MOSI: B1.51, J7.6, J7.12, U$1.P$14 (A14), U$1.P$30 (A14), U$3.10 (SDI), U$4.10 (SDI)
SPI_SS: B1.53
STEP1_1A: J2.1, J2.2, U$3.3 (M1B)
STEP1_1B: J2.3, J2.4, U$3.4 (M1A)
STEP1_2A: J2.5, J2.6, U$3.5 (M2A)
STEP1_2B: J2.7, J2.8, U$3.6 (M2B)
STEP2_1A: J1.1, J1.2, U$4.3 (M1B)
STEP2_1B: J1.3, J1.4, U$4.4 (M1A)
STEP2_2A: J1.5, J1.6, U$4.5 (M2A)
STEP2_2B: J1.7, J1.8, U$4.6 (M2B)
TEMP+: B1.A0 (A0(RX0)), C1.1, J5.1, J5.2, R1.1
TEMP-: C1.2, J5.3, J5.4
T_CS: B1.33, J7.11
T_IRQ: J7.14

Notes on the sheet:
DBT MINI-SHIELD https://github.com/hiiragii/dbt-shield/mini
hiiragii Rev B 9/27/2020
4-bit Input
24V/ 5V Stepdown
Connectors / Headers
100W Mosfets
500mW Mosfets
Arduino Mega R3
TMC2130 Stepper Drivers
104NT Thermistor Input

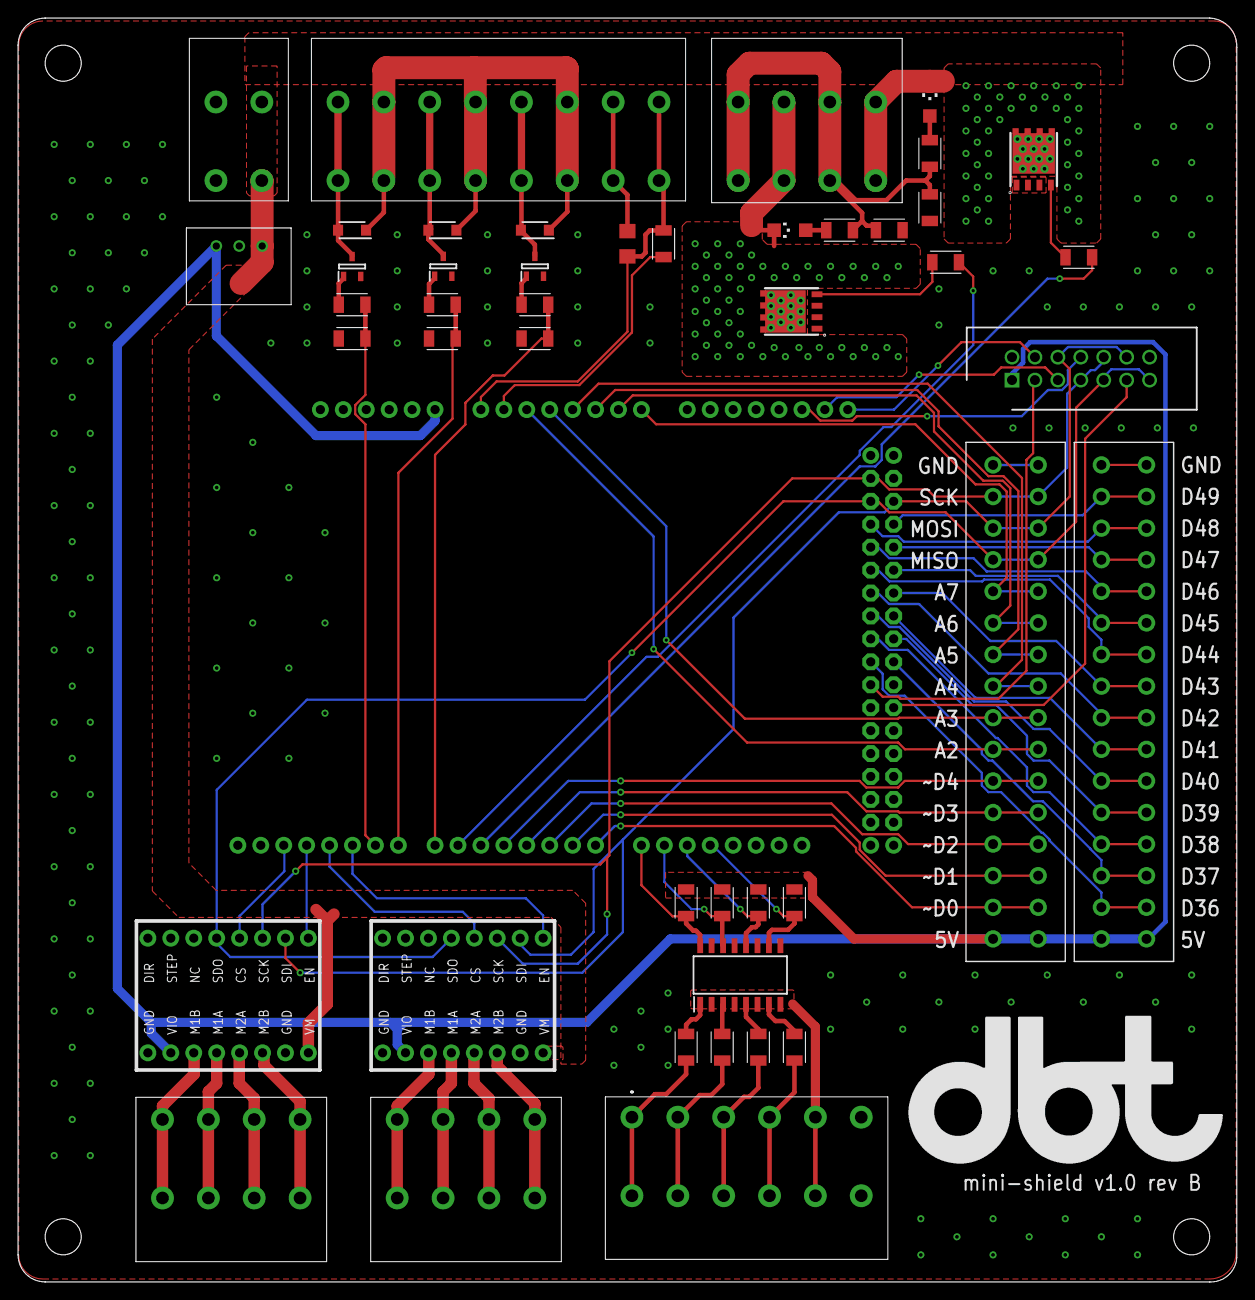
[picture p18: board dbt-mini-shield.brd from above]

Board: 2 copper layers, 135.0 x 140.0 mm, 46 parts (1 on the bottom side), 82 nets.

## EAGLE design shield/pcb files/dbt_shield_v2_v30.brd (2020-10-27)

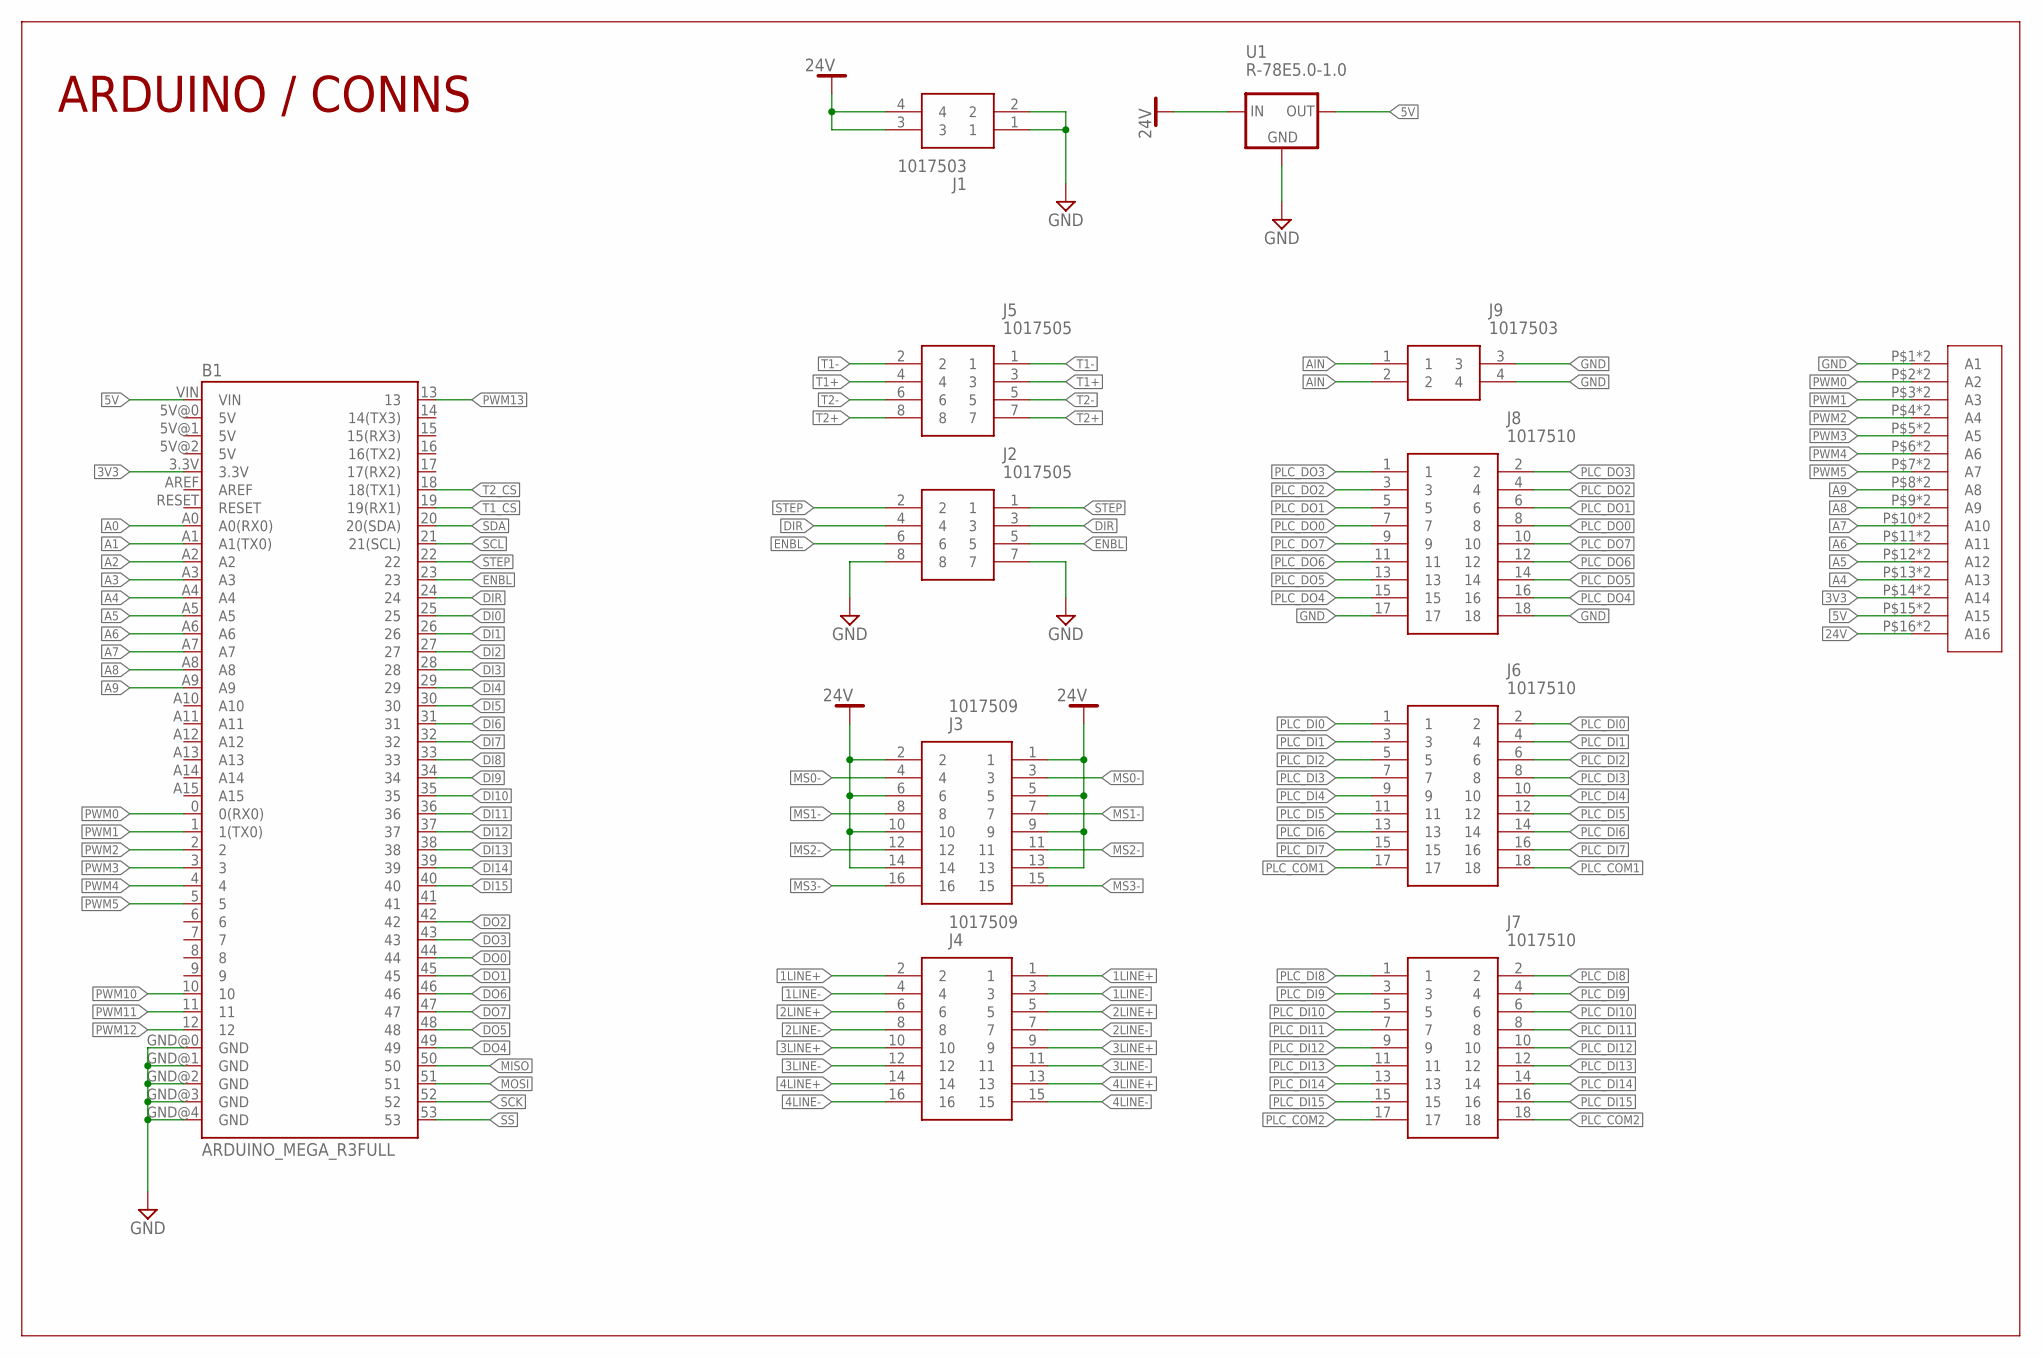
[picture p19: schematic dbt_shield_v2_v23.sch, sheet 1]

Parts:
B1: ARDUINO_MEGA_R3FULL; ARDUINO_MEGA
J1, J9: 1017503
J2, J5: 1017505
J3, J4: 1017509
J6, J7, J8: 1017510; SHDR18W120P870X508_2X9_4652X18
U1: R-78E5.0-1.0; DC-DC_CONVERTER_78XX
U$1: 1861991

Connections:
1LINE+: J4.1, J4.2; also elsewhere on the board
1LINE-: J4.3, J4.4; also elsewhere on the board
2LINE+: J4.5, J4.6; also elsewhere on the board
2LINE-: J4.7, J4.8; also elsewhere on the board
3LINE+: J4.9, J4.10; also elsewhere on the board
3LINE-: J4.11, J4.12; also elsewhere on the board
3V3: B1.3.3V, U$1.P$14 (A14), U$1.P$30 (A14); also elsewhere on the board
4LINE+: J4.13, J4.14; also elsewhere on the board
4LINE-: J4.15, J4.16; also elsewhere on the board
5V: B1.VIN, U1.VOUT (OUT), U$1.P$15 (A15), U$1.P$31 (A15); also elsewhere on the board
24V: J1.3, J1.4, J3.1, J3.2, J3.5, J3.6, J3.9, J3.10, J3.13, J3.14, U1.VIN (IN), U$1.P$16 (A16), U$1.P$32 (A16); also elsewhere on the board
A0: B1.A0 (A0(RX0)); also elsewhere on the board
A1: B1.A1 (A1(TX0)); also elsewhere on the board
A2: B1.A2; also elsewhere on the board
A3: B1.A3; also elsewhere on the board
A4: B1.A4, U$1.P$13 (A13), U$1.P$29 (A13)
A5: B1.A5, U$1.P$12 (A12), U$1.P$28 (A12)
A6: B1.A6, U$1.P$11 (A11), U$1.P$27 (A11)
A7: B1.A7, U$1.P$10 (A10), U$1.P$26 (A10)
A8: B1.A8, U$1.P$9 (A9), U$1.P$25 (A9)
A9: B1.A9, U$1.P$8 (A8), U$1.P$24 (A8)
AIN: J9.1, J9.2; also elsewhere on the board
DI0: B1.25; also elsewhere on the board
DI1: B1.26; also elsewhere on the board
DI2: B1.27; also elsewhere on the board
DI3: B1.28; also elsewhere on the board
DI4: B1.29; also elsewhere on the board
DI5: B1.30; also elsewhere on the board
DI6: B1.31; also elsewhere on the board
DI7: B1.32; also elsewhere on the board
DI8: B1.33; also elsewhere on the board
DI9: B1.34; also elsewhere on the board
DI10: B1.35; also elsewhere on the board
DI11: B1.36; also elsewhere on the board
DI12: B1.37; also elsewhere on the board
DI13: B1.38; also elsewhere on the board
DI14: B1.39; also elsewhere on the board
DI15: B1.40; also elsewhere on the board
DIR: B1.24, J2.3, J2.4
DO0: B1.44; also elsewhere on the board
DO1: B1.45; also elsewhere on the board
DO2: B1.42; also elsewhere on the board
DO3: B1.43; also elsewhere on the board
DO4: B1.49; also elsewhere on the board
DO5: B1.48; also elsewhere on the board
DO6: B1.46; also elsewhere on the board
DO7: B1.47; also elsewhere on the board
ENBL: B1.23, J2.5, J2.6
GND: B1.GND@0 (GND), B1.GND@1 (GND), B1.GND@2 (GND), B1.GND@3 (GND), B1.GND@4 (GND), J1.1, J1.2, J2.7, J2.8, J8.17, J8.18, J9.3, J9.4, U1.GND, U$1.P$1 (A1), U$1.P$17 (A1); also elsewhere on the board
MISO: B1.50; also elsewhere on the board
MOSI: B1.51
MS0-: J3.3, J3.4; also elsewhere on the board
MS1-: J3.7, J3.8; also elsewhere on the board
MS2-: J3.11, J3.12; also elsewhere on the board
MS3-: J3.15, J3.16; also elsewhere on the board
PLC_COM1: J6.17, J6.18; also elsewhere on the board
PLC_COM2: J7.17, J7.18; also elsewhere on the board
PLC_DI0: J6.1, J6.2; also elsewhere on the board
PLC_DI1: J6.3, J6.4; also elsewhere on the board
PLC_DI2: J6.5, J6.6; also elsewhere on the board
PLC_DI3: J6.7, J6.8; also elsewhere on the board
PLC_DI4: J6.9, J6.10; also elsewhere on the board
PLC_DI5: J6.11, J6.12; also elsewhere on the board
PLC_DI6: J6.13, J6.14; also elsewhere on the board
PLC_DI7: J6.15, J6.16; also elsewhere on the board
PLC_DI8: J7.1, J7.2; also elsewhere on the board
PLC_DI9: J7.3, J7.4; also elsewhere on the board
PLC_DI10: J7.5, J7.6; also elsewhere on the board
PLC_DI11: J7.7, J7.8; also elsewhere on the board
PLC_DI12: J7.9, J7.10; also elsewhere on the board
PLC_DI13: J7.11, J7.12; also elsewhere on the board
PLC_DI14: J7.13, J7.14; also elsewhere on the board
PLC_DI15: J7.15, J7.16; also elsewhere on the board
PLC_DO0: J8.7, J8.8; also elsewhere on the board
PLC_DO1: J8.5, J8.6; also elsewhere on the board
PLC_DO2: J8.3, J8.4; also elsewhere on the board
PLC_DO3: J8.1, J8.2; also elsewhere on the board
PLC_DO4: J8.15, J8.16; also elsewhere on the board
PLC_DO5: J8.13, J8.14; also elsewhere on the board
PLC_DO6: J8.11, J8.12; also elsewhere on the board
PLC_DO7: J8.9, J8.10; also elsewhere on the board
PWM0: B1.0 (0(RX0)), U$1.P$2 (A2), U$1.P$18 (A2)
PWM1: B1.1 (1(TX0)), U$1.P$3 (A3), U$1.P$19 (A3)
PWM2: B1.2, U$1.P$4 (A4), U$1.P$20 (A4)
PWM3: B1.3, U$1.P$5 (A5), U$1.P$21 (A5)
PWM4: B1.4, U$1.P$6 (A6), U$1.P$22 (A6)
PWM5: B1.5, U$1.P$7 (A7), U$1.P$23 (A7)
PWM10: B1.10; also elsewhere on the board
PWM11: B1.11; also elsewhere on the board
PWM12: B1.12; also elsewhere on the board
PWM13: B1.13; also elsewhere on the board
SCK: B1.52; also elsewhere on the board
SCL: B1.21 (21(SCL)); also elsewhere on the board
SDA: B1.20 (20(SDA)); also elsewhere on the board
SS: B1.53
STEP: B1.22, J2.1, J2.2
T1+: J5.3, J5.4; also elsewhere on the board
T1-: J5.1, J5.2; also elsewhere on the board
T1_CS: B1.19 (19(RX1)); also elsewhere on the board
T2+: J5.7, J5.8; also elsewhere on the board
T2-: J5.5, J5.6; also elsewhere on the board
T2_CS: B1.18 (18(TX1)); also elsewhere on the board

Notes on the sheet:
ARDUINO / CONNS

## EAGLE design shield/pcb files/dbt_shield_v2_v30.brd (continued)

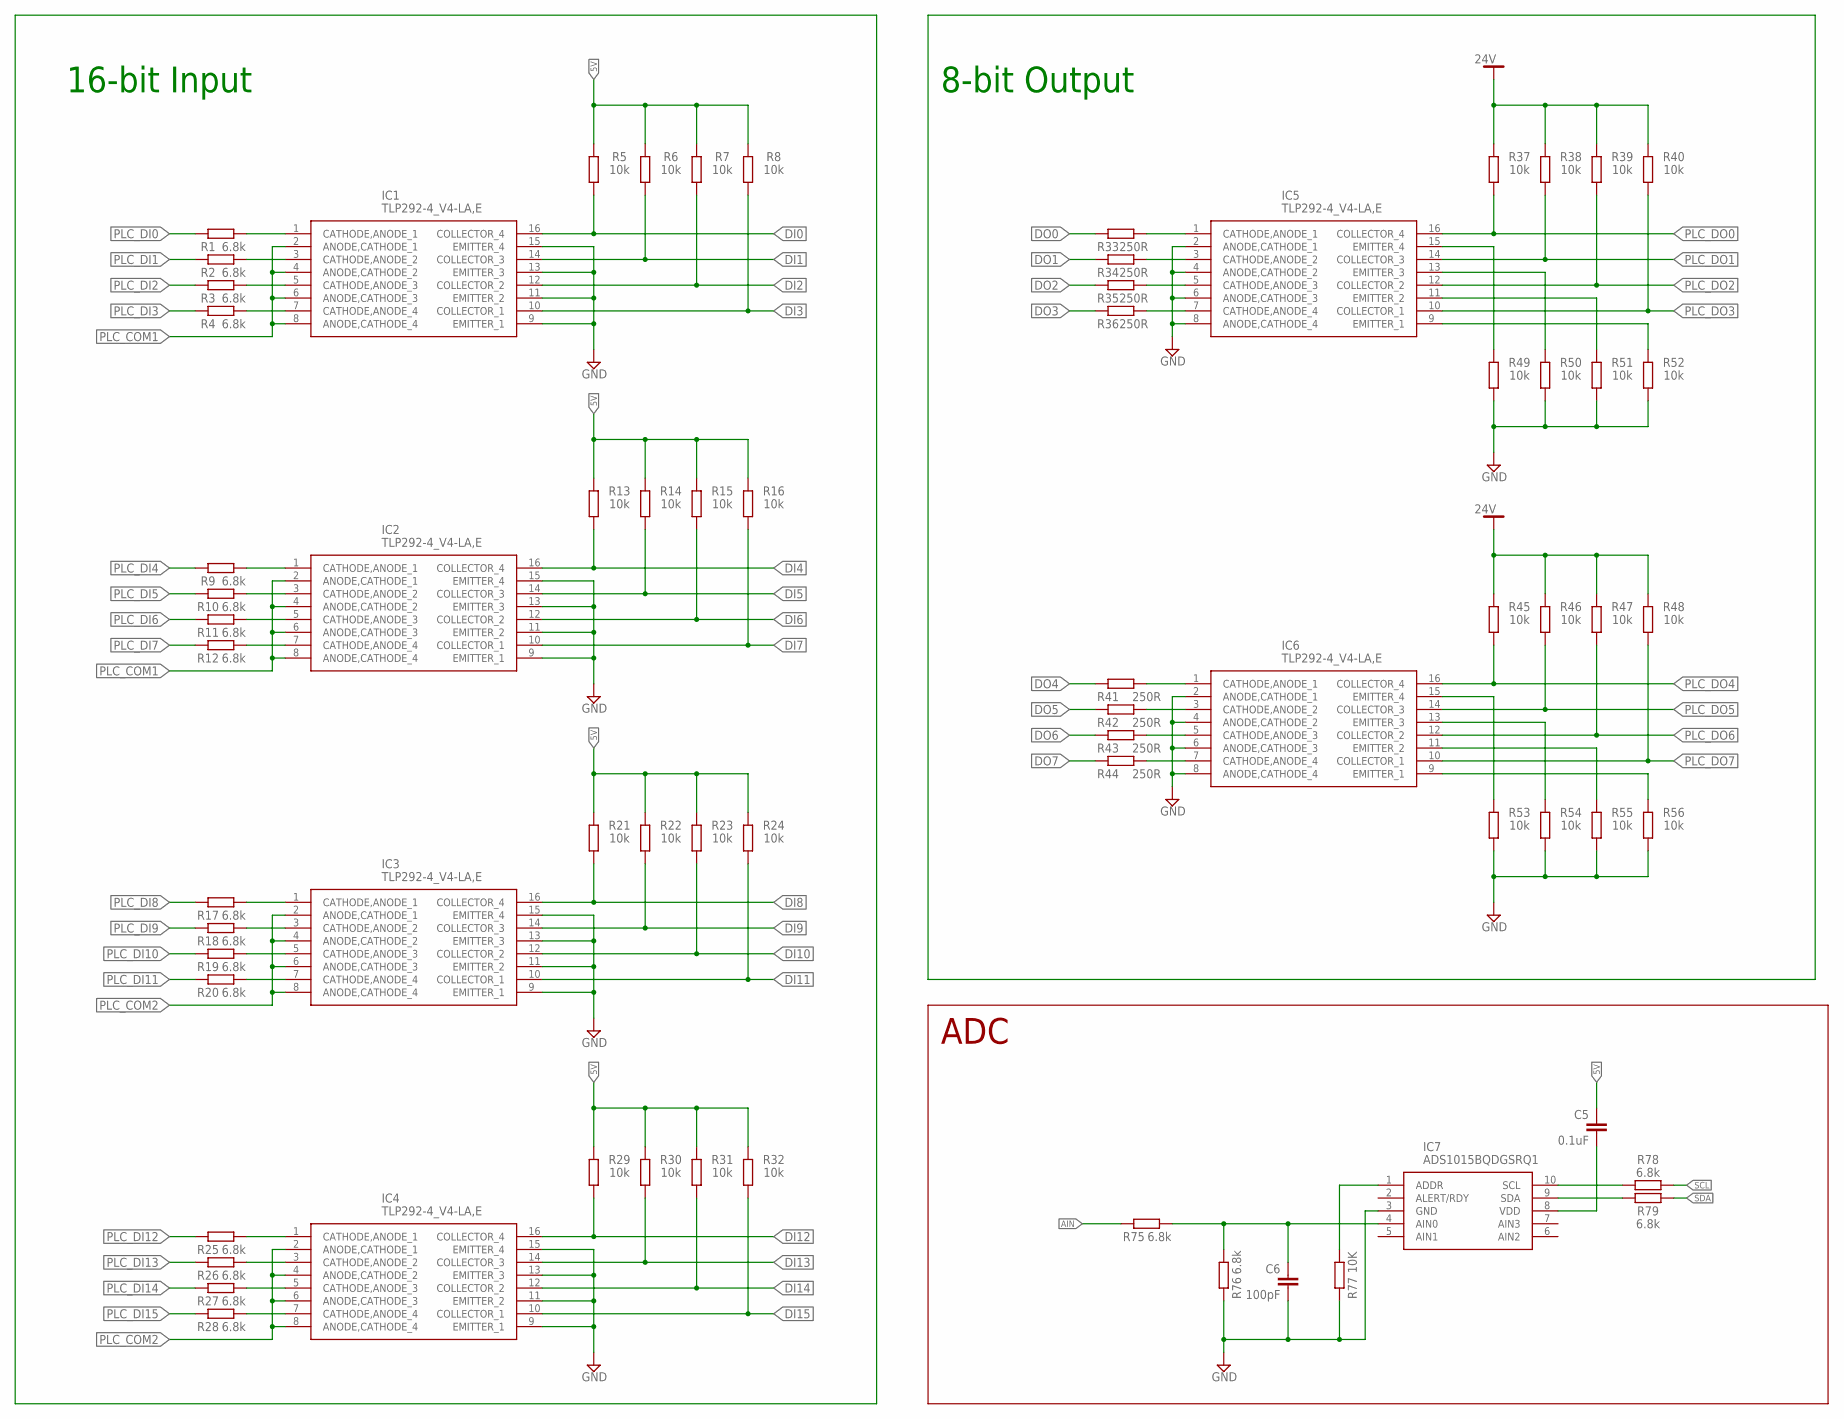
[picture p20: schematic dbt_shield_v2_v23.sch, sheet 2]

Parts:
C5: 0.1uF; CAPC3216X135
C6: 100pF; CAPC3216X135
IC1, IC2, IC3, IC4, IC5, IC6: TLP292-4_V4-LA,E; SOIC127P700X230-16N
IC7: ADS1015BQDGSRQ1; SOP50P490X110-10N
R1, R2, R3, R4, R9, R10, R11, R12, R17, R18, R19, R20, R25, R26, R27, R28, R75, R76, R78, R79: 6.8k; RESC3216X70
R5, R6, R7, R8, R13, R14, R15, R16, R21, R22, R23, R24, R29, R30, R31, R32, R37, R38, R39, R40, R45, R46, R47, R48, R49, R50, R51, R52, R53, R54, R55, R56: 10k; RESC3216X70
R33, R34, R35, R36, R41, R42, R43, R44: 250R; RESC3216X70
R77: 10K; RESC3216X70

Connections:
5V: C5.1, R5.2, R6.2, R7.2, R8.2, R13.2, R14.2, R15.2, R16.2, R21.2, R22.2, R23.2, R24.2, R29.2, R30.2, R31.2, R32.2; also elsewhere on the board
24V: R37.2, R38.2, R39.2, R40.2, R45.2, R46.2, R47.2, R48.2; also elsewhere on the board
AIN: R75.1; also elsewhere on the board
DI0: IC1.16 (COLLECTOR_4), R5.1; also elsewhere on the board
DI1: IC1.14 (COLLECTOR_3), R6.1; also elsewhere on the board
DI2: IC1.12 (COLLECTOR_2), R7.1; also elsewhere on the board
DI3: IC1.10 (COLLECTOR_1), R8.1; also elsewhere on the board
DI4: IC2.16 (COLLECTOR_4), R13.1; also elsewhere on the board
DI5: IC2.14 (COLLECTOR_3), R14.1; also elsewhere on the board
DI6: IC2.12 (COLLECTOR_2), R15.1; also elsewhere on the board
DI7: IC2.10 (COLLECTOR_1), R16.1; also elsewhere on the board
DI8: IC3.16 (COLLECTOR_4), R21.1; also elsewhere on the board
DI9: IC3.14 (COLLECTOR_3), R22.1; also elsewhere on the board
DI10: IC3.12 (COLLECTOR_2), R23.1; also elsewhere on the board
DI11: IC3.10 (COLLECTOR_1), R24.1; also elsewhere on the board
DI12: IC4.16 (COLLECTOR_4), R29.1; also elsewhere on the board
DI13: IC4.14 (COLLECTOR_3), R30.1; also elsewhere on the board
DI14: IC4.12 (COLLECTOR_2), R31.1; also elsewhere on the board
DI15: IC4.10 (COLLECTOR_1), R32.1; also elsewhere on the board
DO0: R33.1; also elsewhere on the board
DO1: R34.1; also elsewhere on the board
DO2: R35.1; also elsewhere on the board
DO3: R36.1; also elsewhere on the board
DO4: R41.1; also elsewhere on the board
DO5: R42.1; also elsewhere on the board
DO6: R43.1; also elsewhere on the board
DO7: R44.1; also elsewhere on the board
GND: C6.2, IC1.9 (EMITTER_1), IC1.11 (EMITTER_2), IC1.13 (EMITTER_3), IC1.15 (EMITTER_4), IC2.9 (EMITTER_1), IC2.11 (EMITTER_2), IC2.13 (EMITTER_3), IC2.15 (EMITTER_4), IC3.9 (EMITTER_1), IC3.11 (EMITTER_2), IC3.13 (EMITTER_3), IC3.15 (EMITTER_4), IC4.9 (EMITTER_1), IC4.11 (EMITTER_2), IC4.13 (EMITTER_3), IC4.15 (EMITTER_4), IC5.2 (ANODE,CATHODE_1), IC5.4 (ANODE,CATHODE_2), IC5.6 (ANODE,CATHODE_3), IC5.8 (ANODE,CATHODE_4), IC6.2 (ANODE,CATHODE_1), IC6.4 (ANODE,CATHODE_2), IC6.6 (ANODE,CATHODE_3), IC6.8 (ANODE,CATHODE_4), IC7.3 (GND), R49.1, R50.1, R51.1, R52.1, R53.1, R54.1, R55.1, R56.1, R76.1, R77.1; also elsewhere on the board
unnamed: IC1.1 (CATHODE,ANODE_1), R1.2
unnamed: IC1.3 (CATHODE,ANODE_2), R2.2
unnamed: IC1.5 (CATHODE,ANODE_3), R3.2
unnamed: IC1.7 (CATHODE,ANODE_4), R4.2
unnamed: IC2.1 (CATHODE,ANODE_1), R9.2
unnamed: IC2.3 (CATHODE,ANODE_2), R10.2
unnamed: IC2.5 (CATHODE,ANODE_3), R11.2
unnamed: IC2.7 (CATHODE,ANODE_4), R12.2
unnamed: IC3.1 (CATHODE,ANODE_1), R17.2
unnamed: IC3.3 (CATHODE,ANODE_2), R18.2
unnamed: IC3.5 (CATHODE,ANODE_3), R19.2
unnamed: IC3.7 (CATHODE,ANODE_4), R20.2
unnamed: IC4.1 (CATHODE,ANODE_1), R25.2
unnamed: IC4.3 (CATHODE,ANODE_2), R26.2
unnamed: IC4.5 (CATHODE,ANODE_3), R27.2
unnamed: IC4.7 (CATHODE,ANODE_4), R28.2
unnamed: IC5.1 (CATHODE,ANODE_1), R33.2
unnamed: IC5.3 (CATHODE,ANODE_2), R34.2
unnamed: IC5.5 (CATHODE,ANODE_3), R35.2
unnamed: IC5.7 (CATHODE,ANODE_4), R36.2
unnamed: IC6.1 (CATHODE,ANODE_1), R41.2
unnamed: IC6.3 (CATHODE,ANODE_2), R42.2
unnamed: IC6.5 (CATHODE,ANODE_3), R43.2
unnamed: IC6.7 (CATHODE,ANODE_4), R44.2
unnamed: IC5.15 (EMITTER_4), R49.2
unnamed: IC5.13 (EMITTER_3), R50.2
unnamed: IC5.11 (EMITTER_2), R51.2
unnamed: IC5.9 (EMITTER_1), R52.2
unnamed: IC6.15 (EMITTER_4), R53.2
unnamed: IC6.13 (EMITTER_3), R54.2
unnamed: IC6.11 (EMITTER_2), R55.2
unnamed: IC6.9 (EMITTER_1), R56.2
unnamed: C6.1, IC7.4 (AIN0), R75.2, R76.2
unnamed: IC7.1 (ADDR), R77.2
unnamed: C5.2, IC7.8 (VDD)
unnamed: IC7.9 (SDA), R79.2
unnamed: IC7.10 (SCL), R78.2
PLC_COM1: IC1.2 (ANODE,CATHODE_1), IC1.4 (ANODE,CATHODE_2), IC1.6 (ANODE,CATHODE_3), IC1.8 (ANODE,CATHODE_4), IC2.2 (ANODE,CATHODE_1), IC2.4 (ANODE,CATHODE_2), IC2.6 (ANODE,CATHODE_3), IC2.8 (ANODE,CATHODE_4); also elsewhere on the board
PLC_COM2: IC3.2 (ANODE,CATHODE_1), IC3.4 (ANODE,CATHODE_2), IC3.6 (ANODE,CATHODE_3), IC3.8 (ANODE,CATHODE_4), IC4.2 (ANODE,CATHODE_1), IC4.4 (ANODE,CATHODE_2), IC4.6 (ANODE,CATHODE_3), IC4.8 (ANODE,CATHODE_4); also elsewhere on the board
PLC_DI0: R1.1; also elsewhere on the board
PLC_DI1: R2.1; also elsewhere on the board
PLC_DI2: R3.1; also elsewhere on the board
PLC_DI3: R4.1; also elsewhere on the board
PLC_DI4: R9.1; also elsewhere on the board
PLC_DI5: R10.1; also elsewhere on the board
PLC_DI6: R11.1; also elsewhere on the board
PLC_DI7: R12.1; also elsewhere on the board
PLC_DI8: R17.1; also elsewhere on the board
PLC_DI9: R18.1; also elsewhere on the board
PLC_DI10: R19.1; also elsewhere on the board
PLC_DI11: R20.1; also elsewhere on the board
PLC_DI12: R25.1; also elsewhere on the board
PLC_DI13: R26.1; also elsewhere on the board
PLC_DI14: R27.1; also elsewhere on the board
PLC_DI15: R28.1; also elsewhere on the board
PLC_DO0: IC5.16 (COLLECTOR_4), R37.1; also elsewhere on the board
PLC_DO1: IC5.14 (COLLECTOR_3), R38.1; also elsewhere on the board
PLC_DO2: IC5.12 (COLLECTOR_2), R39.1; also elsewhere on the board
PLC_DO3: IC5.10 (COLLECTOR_1), R40.1; also elsewhere on the board
PLC_DO4: IC6.16 (COLLECTOR_4), R45.1; also elsewhere on the board
PLC_DO5: IC6.14 (COLLECTOR_3), R46.1; also elsewhere on the board
PLC_DO6: IC6.12 (COLLECTOR_2), R47.1; also elsewhere on the board
PLC_DO7: IC6.10 (COLLECTOR_1), R48.1; also elsewhere on the board
SCL: R78.1; also elsewhere on the board
SDA: R79.1; also elsewhere on the board

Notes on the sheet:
16-bit Input
8-bit Output
ADC

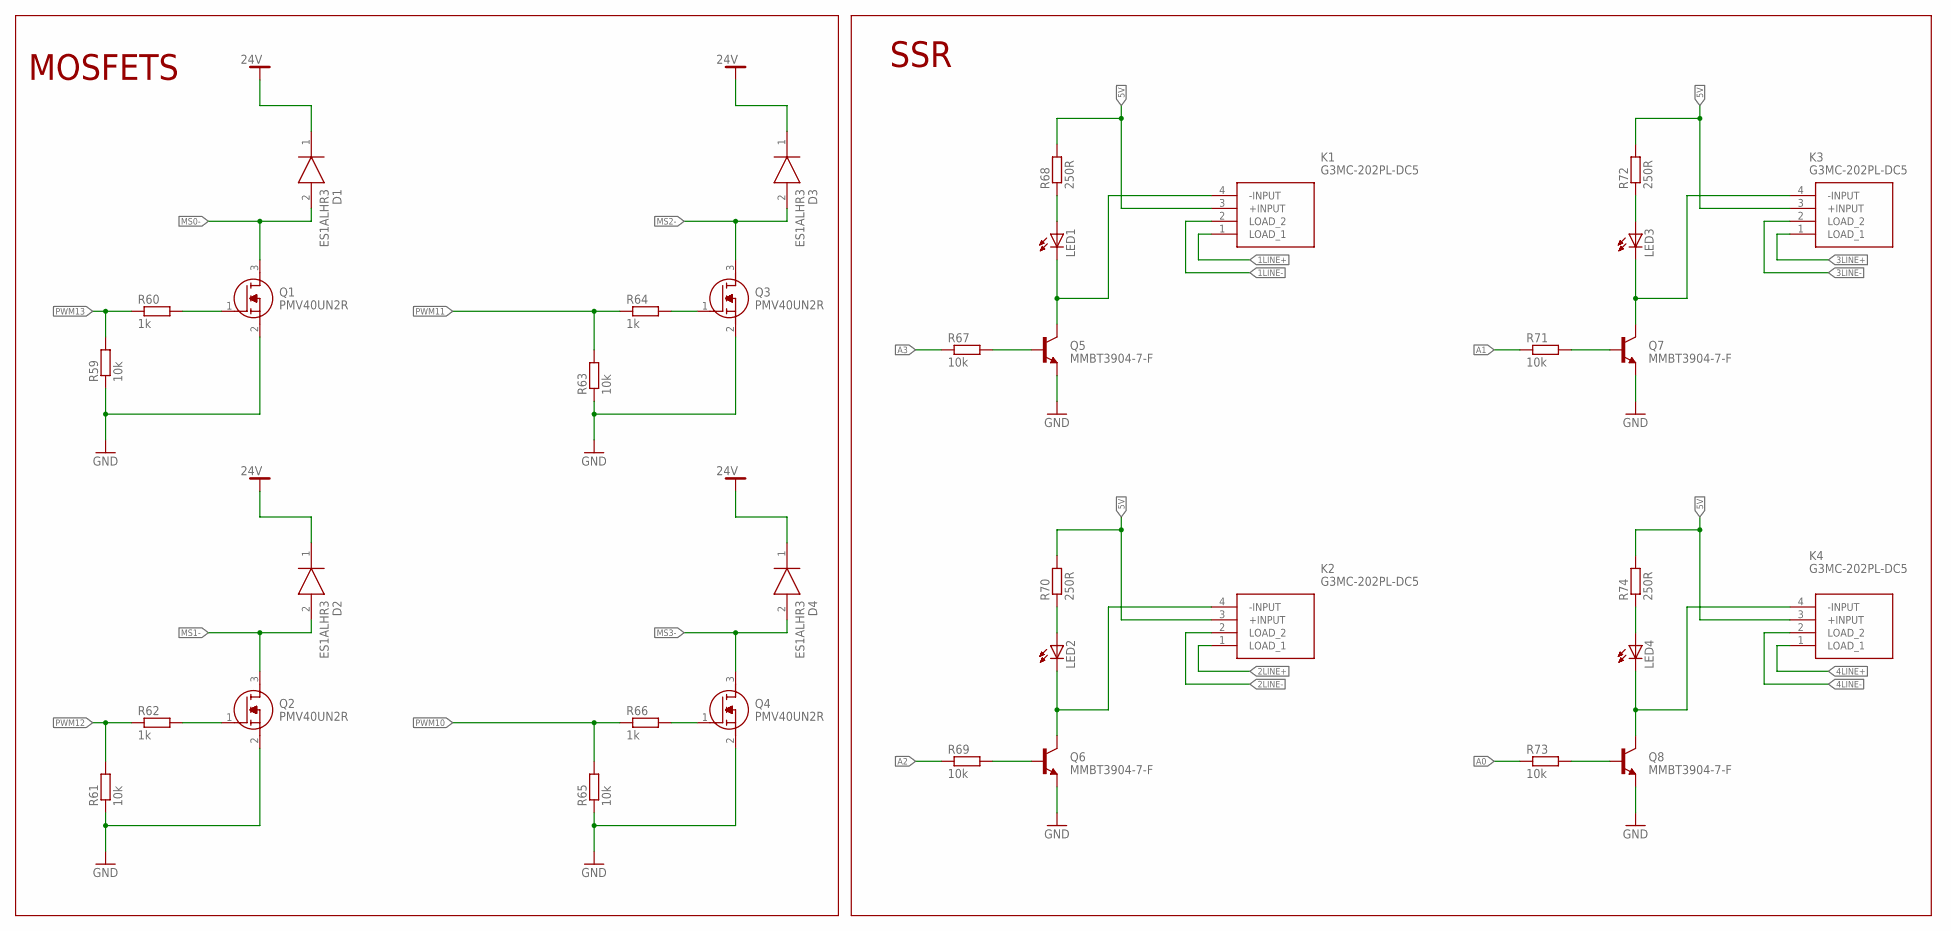
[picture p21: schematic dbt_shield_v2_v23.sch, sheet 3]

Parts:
D1, D2, D3, D4: ES1ALHR3; SODFL3618X143N
K1, K2, K3, K4: G3MC-202PL-DC5; G3MC202PLDC5
LED1, LED2, LED3, LED4: LEDCHIPLED_1206; CHIPLED_1206
Q1, Q2, Q3, Q4: PMV40UN2R; SOT95P230X110-3N
Q5, Q6, Q7, Q8: MMBT3904-7-F; SOT95P230X110-3N1
R59, R61, R63, R65, R67, R69, R71, R73: 10k; RESC3216X70
R60, R62, R64, R66: 1k; RESC3216X70
R68, R70, R72, R74: 250R; RESC3216X70

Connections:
1LINE+: K1.1 (LOAD_1); also elsewhere on the board
1LINE-: K1.2 (LOAD_2); also elsewhere on the board
2LINE+: K2.1 (LOAD_1); also elsewhere on the board
2LINE-: K2.2 (LOAD_2); also elsewhere on the board
3LINE+: K3.1 (LOAD_1); also elsewhere on the board
3LINE-: K3.2 (LOAD_2); also elsewhere on the board
4LINE+: K4.1 (LOAD_1); also elsewhere on the board
4LINE-: K4.2 (LOAD_2); also elsewhere on the board
5V: K1.3 (+INPUT), K2.3 (+INPUT), K3.3 (+INPUT), K4.3 (+INPUT), R68.2, R70.2, R72.2, R74.2; also elsewhere on the board
24V: D1.1 (K), D2.1 (K), D3.1 (K), D4.1 (K); also elsewhere on the board
A0: R73.1; also elsewhere on the board
A1: R71.1; also elsewhere on the board
A2: R69.1; also elsewhere on the board
A3: R67.1; also elsewhere on the board
GND: Q1.2 (S), Q2.2 (S), Q3.2 (S), Q4.2 (S), Q5.E, Q6.E, Q7.E, Q8.E, R59.1, R61.1, R63.1, R65.1; also elsewhere on the board
MS0-: D1.2 (A), Q1.3 (D); also elsewhere on the board
MS1-: D2.2 (A), Q2.3 (D); also elsewhere on the board
MS2-: D3.2 (A), Q3.3 (D); also elsewhere on the board
MS3-: D4.2 (A), Q4.3 (D); also elsewhere on the board
unnamed: Q1.1 (G), R60.2
unnamed: Q2.1 (G), R62.2
unnamed: Q3.1 (G), R64.2
unnamed: Q4.1 (G), R66.2
unnamed: LED1.A, R68.1
unnamed: K1.4 (-INPUT), LED1.C, Q5.C
unnamed: Q5.B, R67.2
unnamed: LED2.A, R70.1
unnamed: K2.4 (-INPUT), LED2.C, Q6.C
unnamed: Q6.B, R69.2
unnamed: LED3.A, R72.1
unnamed: K3.4 (-INPUT), LED3.C, Q7.C
unnamed: Q7.B, R71.2
unnamed: LED4.A, R74.1
unnamed: K4.4 (-INPUT), LED4.C, Q8.C
unnamed: Q8.B, R73.2
PWM10: R65.2, R66.1; also elsewhere on the board
PWM11: R63.2, R64.1; also elsewhere on the board
PWM12: R61.2, R62.1; also elsewhere on the board
PWM13: R59.2, R60.1; also elsewhere on the board

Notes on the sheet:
MOSFETS
SSR

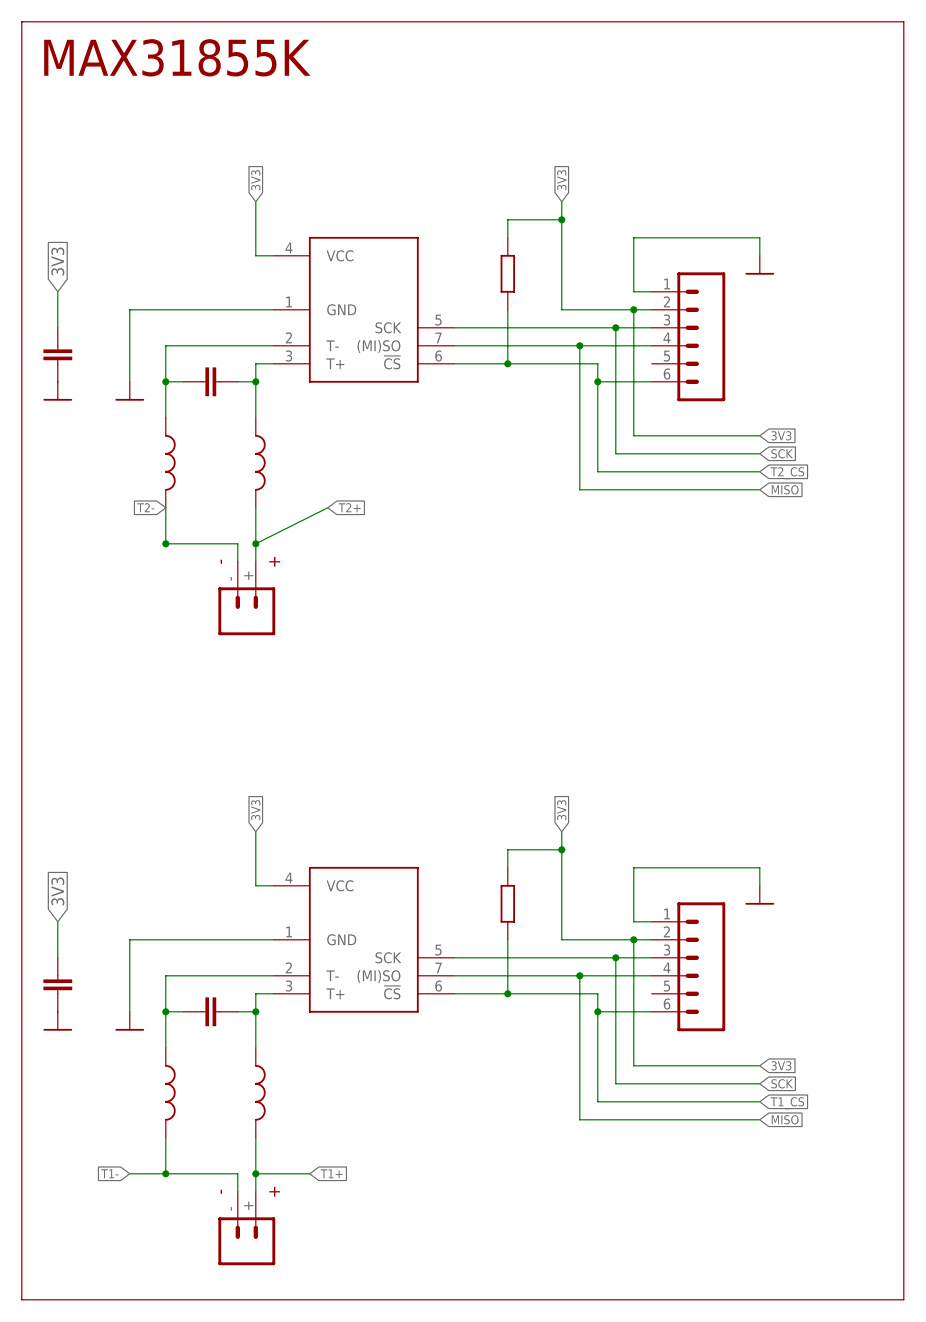
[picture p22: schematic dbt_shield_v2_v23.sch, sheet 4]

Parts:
C1, C3: 0.1uF; CAPC3216X135
C2, C4: 10 nF; CAPC3216X135
JP1, JP3: DNP; 1X06
JP2, JP4: PCB_THERMOCOUPLE; PCC-SMP
L1, L2, L3, L4: 470 OHM; INDC3216X190
R57, R58: 10k; RESC3216X70
U2, U3: MAX31855K; SOIC8

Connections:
3V3: C1.1, C3.1, JP1.2, JP3.2, R57.2, R58.2, U2.4 (VCC), U3.4 (VCC); also elsewhere on the board
GND: C1.2, C3.2, JP1.1, JP3.1, U2.1 (GND), U3.1 (GND); also elsewhere on the board
MISO: JP1.4, JP3.4, U2.7 ((MI)SO), U3.7 ((MI)SO); also elsewhere on the board
unnamed: C2.1, L2.1, U2.3 (T+)
unnamed: C4.1, L4.1, U3.3 (T+)
unnamed: C4.2, L3.1, U3.2 (T-)
unnamed: C2.2, L1.1, U2.2 (T-)
SCK: JP1.3, JP3.3, U2.5 (SCK), U3.5 (SCK); also elsewhere on the board
T1+: JP2.+, L2.2; also elsewhere on the board
T1-: JP2.-, L1.2; also elsewhere on the board
T1_CS: JP1.6, R57.1, U2.6 (!CS); also elsewhere on the board
T2+: JP4.+, L4.2; also elsewhere on the board
T2-: JP4.-, L3.2; also elsewhere on the board
T2_CS: JP3.6, R58.1, U3.6 (!CS); also elsewhere on the board

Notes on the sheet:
MAX31855K

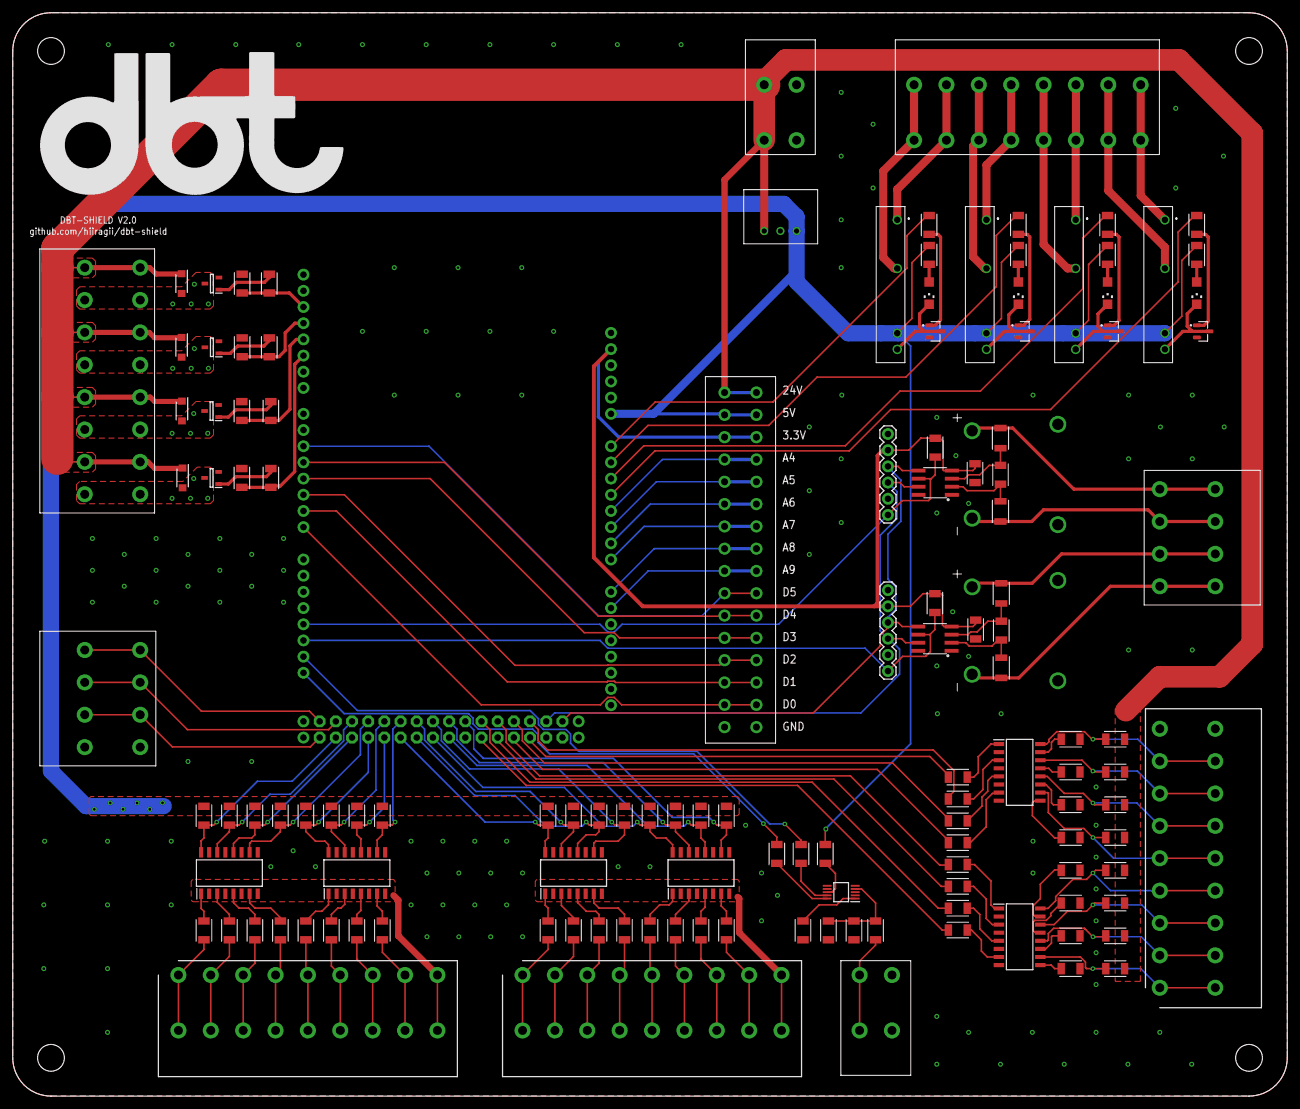
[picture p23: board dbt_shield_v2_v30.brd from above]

Board: 2 copper layers, 200.0 x 170.0 mm, 134 parts (1 on the bottom side), 157 nets.

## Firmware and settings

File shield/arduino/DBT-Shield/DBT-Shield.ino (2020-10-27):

/********************************************************
 * PID RelayOutput Example
 * Same as basic example, except that this time, the output
 * is going to a digital pin which (we presume) is controlling
 * a relay.  the pid is designed to Output an analog value,
 * but the relay can only be On/Off.
 *
 *   to connect them together we use "time proportioning
 * control"  it's essentially a really slow version of PWM.
 * first we decide on a window size (5000mS say.) we then
 * set the pid to adjust its output between 0 and that window
 * size.  lastly, we add some logic that translates the PID
 * output into "Relay On Time" with the remainder of the
 * window being "Relay Off Time"
 ********************************************************/

#include <PID_v1.h>
#include "pins.h"
#include <SPI.h>
#include "Adafruit_MAX31855.h"
#include <ClearPathMotorSD.h>
#include <ClearPathStepGen.h>

/********************************************************
 * PID
 ********************************************************/
//Define Variables we'll be connecting to
double Setpoint, Input, Output;
//Specify the links and initial tuning parameters
double Kp=2, Ki=5, Kd=1;
PID myPID(&Input, &Output, &Setpoint, Kp, Ki, Kd, DIRECT);

const int WindowSize = 2000;
unsigned long windowStartTime;
unsigned long time_1 = 0;
char buffer[64];
int sofar;
float mm, fr, flow, tempt;
bool heaterOn = false;

/********************************************************
 * THERMOCOUPLE
 ********************************************************/
Adafruit_MAX31855 t1 (SCK, T2_CS, MISO);

byte BSPEED = 0b00000000;
int IN_PINS[] = {IN_b0, IN_b1, IN_b2, IN_b3, IN_b4, IN_b5, IN_b6, IN_b7};
unsigned int TOOL_SPEED = 0;

void updateSpeed (){
  for(int i=0; i<7; i++){
    bitWrite(BSPEED,i, digitalRead(IN_PINS[i]));
  }
  TOOL_SPEED = (unsigned int)BSPEED;
}


/********************************************************
 * MOTOR
 ********************************************************/
ClearPathMotorSD Extruder;
ClearPathStepGen machine(&Extruder);

void help(){
  Serial.print("G1 [E(mm)] [F(mm/s)]; - linear move");
  Serial.println("G6 [F(mm/s)]; - move w/ speed");
  Serial.println("M18; - disable motors");
  Serial.println("M104 [R(temperature)]; - set extruder temperature");
  Serial.println("M108; - cancel heating");
  Serial.println("M111; [R(flow)]- flow multiplier *1%");
  Serial.println("M100; -help");
}

void ready() {
  sofar=0; // clear input buffer
  //Serial.print(F("> ")); // signal ready to receive input
}

float parseNumber(char code,float val) {
  char *ptr=buffer;  // start at the beginning of buffer
  while((long)ptr > 1 && (*ptr) && (long)ptr < (long)buffer+sofar) {  // walk to the end
    if(*ptr==code) {  // if you find code on your walk,
      return atof(ptr+1);  // convert the digits that follow into a float and return it
    }
    ptr=strchr(ptr,' ')+1;  // take a step from here to the letter after the next space
  }
  return val;  // end reached, nothing found, return default val.
}

void processCommand(){
  // look for commands that start with 'G'
  int cmd=parseNumber('G',-1);
  switch(cmd) {
  case 1: // move to distance
    if(Input > Setpoint-10){
      Extruder.setMaxVel(parseNumber('F', fr));
      Extruder.move(parseNumber('E', mm));
    }else{
      Serial.println("COLD EXTRUSION PREVENTED");
    }
    break;
  case 4: // move with speed
    if(Input > Setpoint-10){
    Extruder.moveWithVelocity(parseNumber('F', fr));
    }else{
      Serial.println("COLD EXTRUSION PREVENTED");      
    }
    break; 
    case 69:
      TOOL_SPEED = TOOL_SPEED + 10;
    break;
  default: break;
  }

  // look for commands that start with 'M'
  cmd=parseNumber('M',-1);
  switch(cmd) {
  case 18: // turns off power to steppers (releases the grip)
    Extruder.stopMove();
    break;
  case 100: help(); break;
  case 104:
    Setpoint = parseNumber('R', Setpoint); 
    break;
  case 105:
    heaterOn = true; break;
  case 108:
    heaterOn = false; break;
  case 110:
    digitalWrite(13, HIGH); break;
  case 111:
    flow = parseNumber('R', flow);
  default: break;
  } 
}

void print_stat(){
    // T = temp , S = speed , H = heateron , 
    Serial.print("T");
    Serial.println(Input);


    Serial.print("S");
    Serial.println(TOOL_SPEED);

    Serial.print("H");
    Serial.println(heaterOn);

    //Serial.print("test");
    //Serial.println(BSPEED);

    Serial.print("");

}

void setup()
{
  pinMode(SSR_0_PIN, OUTPUT);
  pinMode(MOSFET_0_PIN, OUTPUT);
  pinMode(13, OUTPUT);
  pinMode(IN_b0, INPUT);
  pinMode(IN_b1, INPUT);
  pinMode(IN_b2, INPUT);
  pinMode(IN_b3, INPUT);
  pinMode(IN_b4, INPUT);
  pinMode(IN_b5, INPUT);
  pinMode(IN_b6, INPUT);
  pinMode(IN_b7, INPUT);

  digitalWrite(13, HIGH);

  Serial.begin(9600);

  help();
  ready();

  Extruder.attach(MOT_DIR_PIN, MOT_STEP_PIN, MOT_ENBL_PIN);
  Extruder.setMaxVel(100000);
  Extruder.setMaxAccel(2000000);
  Extruder.enable();
  machine.Start();

  windowStartTime = millis();
  //initialize the variables we're linked to
  Setpoint = 60;

  //tell the PID to range between 0 and the full window size
  myPID.SetOutputLimits(0, WindowSize);

  //turn the PID on
  myPID.SetMode(AUTOMATIC);

  Input = t1.readCelsius();
  flow = 1.0;
  /*
  Serial.print("Initializing sensor...");
  if (!t1.begin()) {
    Serial.println("ERROR.");
  }*/
}

void loop()
{

  if(Serial.available()){
    char c = Serial.read();

    if(sofar < 64) buffer[sofar++] = c;
    if((c=='\n') || (c == '\r')){
      buffer[sofar] = 0;
      Serial.print(F("\r\n"));
      processCommand();
      ready();
    }
  }
  
  if(heaterOn){
    
    //Input = t1.readCelsius();
    myPID.Compute();
    /************************************************
    * turn the output pin on/off based on pid output
    ************************************************/
    if (millis() - windowStartTime > WindowSize)
    { //time to shift the Relay Window
      windowStartTime += WindowSize;
    }
    if (Output < millis() - windowStartTime){
      digitalWrite(SSR_0_PIN, HIGH);
      Serial.println("HEATER ON");
      //Serial.println(Output);
    }else{
      digitalWrite(SSR_0_PIN, LOW);
    } 
  }
  
  if(millis() > time_1 + 1000){
    time_1 = millis();
    tempt = t1.readCelsius();
    if(!isnan(tempt)){
    Input = tempt;
    }
    print_stat();
    updateSpeed();

    digitalWrite(13, HIGH);
  }
    
  
}

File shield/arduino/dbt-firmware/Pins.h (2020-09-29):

#ifndef _HEADERFILE_H
#define _HEADERFILE_H



#define SSR_0_PIN                             A0
#define SSR_1_PIN                             A1
#define SSR_2_PIN                             A2
#define SSR_3_PIN                             A3


#define MOSFET_0_PIN                          10
#define MOSFET_1_PIN                          11
#define MOSFET_2_PIN                          12
#define MOSFET_3_PIN                          13


#define IN_b0                                 25
#define IN_b1                                 26
#define IN_b2                                 27
#define IN_b3                                 28
#define IN_b4                                 29
#define IN_b5                                 30
#define IN_b6                                 31
#define IN_b7                                 32
#define IN_b8                                 33
#define IN_b9                                 34
#define IN_b10                                35
#define IN_b11                                36
#define IN_b12                                37
#define IN_b13                                38
#define IN_b14                                39
#define IN_b15                                40


#define OUT_b0                                44
#define OUT_b1                                45
#define OUT_b2                                42
#define OUT_b3                                43
#define OUT_b4                                49
#define OUT_b5                                48
#define OUT_b6                                46
#define OUT_b7                                47


#define MOT_STEP_PIN                          22
#define MOT_DIR_PIN                           24
#define MOT_ENBL_PIN                          23


#define MISO                                  50
#define SCK                                   52


#define T1_CS                                 19
#define T2_CS                                 18

#define HEADER_D_0                            0
#define HEADER_D_1                            1
#define HEADER_D_2                            2
#define HEADER_D_3                            3
#define HEADER_D_4                            4
#define HEADER_D_5                            5
#define HEADER_A_0                            A0
#define HEADER_A_1                            A1
#define HEADER_A_2                            A2
#define HEADER_A_3                            A3
#define HEADER_A_4                            A4
#define HEADER_A_5                            A5

#endif // _HEADERFILE_H 

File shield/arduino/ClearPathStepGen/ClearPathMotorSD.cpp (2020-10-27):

/*
  ClearPathMotorSD.h - Library for interfacing with Clearpath-SD motors using an Arduino- Version 1
  Teknic 2017 Brendan Flosenzier

  Copyright (c) 2017 Teknic Inc. This work is free to use, copy and distribute under the terms of the standard
  MIT permissive software license which can be found at https://opensource.org/licenses/MIT

  This library is distributed in the hope that it will be useful,
  but WITHOUT ANY WARRANTY; without even the implied warranty of
  MERCHANTABILITY or FITNESS FOR A PARTICULAR PURPOSE.
*/

/*

  A ClearPathMotorSD is activated by creating an instance of the ClearPathMotorSD class.

  There can several instances of ClearPathMotorSD however each must be attached to different pins.

  This class is used in conjuntion with the ClearPathStepGen class which manages and sends step pulses to each motor.

  Note: Each attached motor must have its direction/B pin connected to one of pins 8-13 on an arduino UNO (PORTB)
  in order to work with the ClearPathStepGen object.  Other devices can be connected to pins 8-13 as well.
  If you are using another Arduino besides the UNO, the ClearPathStepGen must be modifyed to use a different port.

  The functions for a ClearPathMotorSD are:

   ClearPathMotorSD - default constructor for initializing the motor

   attach() - Attachs pins to this motor, and declares them as input/outputs

   stopMove()  - Interupts the current move, the motor may abruptly stop

   move() - sets the maximum veloctiy

   disable() - disables the motor

   enable() - enables the motor

   getCommandedPosition() - Returns the absolute cmomanded position where the position on enable=0

   readHLFB() - Returns the value of the motor's HLFB Pin

   setMaxVel() - sets the maximum veloctiy

   setMaxAccel() - sets the acceleration

   commandDone() - returns wheter or not there is a valid current command

 */
#include "Arduino.h"
#include "ClearPathMotorSD.h"


/*
	This is an internal Function used by ClearPathStepGen to calculate how many pulses to send to each motor.
	It tracks the current command, as well as how many steps have been sent, and calculates how many steps
	to send in the next ISR.
*/
int ClearPathMotorSD::calcSteps()
{
	_TX++;//increment time
	if(!Enabled)
		return 0;

	// Process current move state.
	switch(moveStateX){
		case 3: // IdleState state, executed only once.

			if(CommandX == 0) //If no/finished command/, do nothing set everything to 0
			{
				MovePosnQx=0;
				VelRefQx=0;
				StepsSent=0;
				_TX=0;
				_TX1=0;
				_TX2=0;
				_TX3=0;
				_BurstX=0;
			}
			else
			{
				// Compute Move parameters
				TargetPosnQx = CommandX<<fractionalBits;
				TriangleMovePeakQx = abs(TargetPosnQx>>1);
				if(TargetPosnQx > 0)
					AccelRefQxS = AccLimitQx;
				else
					AccelRefQxS = -AccLimitQx;
				AccelRefQx = AccelRefQxS;
				// Do immediate move if half move length <= maximum acceleration.
				if(TriangleMovePeakQx <= AccLimitQx) {
					AccelRefQx = 0;
					VelRefQx = 0;
					MovePosnQx = TargetPosnQx;
					moveStateX = 3;	//Set to Move Idle
					CommandX=0;		//Zero command
					break;
				}
				// Otherwise, execute move and go to Phase1
				MovePosnQx = MovePosnQx + VelRefQx;// + (AccelRefQx>>1);
				VelRefQx = VelRefQx + AccelRefQx;
				moveStateX = 1;
			}
			break;

		case 1:		//Phase 1 first half of move

			// Execute move
			MovePosnQx = MovePosnQx + VelRefQx + (AccelRefQx>>1);
			VelRefQx = VelRefQx + AccelRefQx;

			// Check position.
			if(abs(MovePosnQx) >= TriangleMovePeakQx) {
				// If half move reached, compute time parameters and go to PXhase2

				if(_flag)		//This makes sure you go one step past half in order to make sure Phase 2 goes well
				{
					if(_TX1 == 0) {
						_TX1 = _TX;
					}
					if(_TX2 == 0) {
						_TX2 = _TX;
					}
					AccelRefQx = -AccelRefQx;					//Set deccelleration
					_TX3 = (_TX2<<1) - _TX1;	//compute time params
					_TAUX = _TX2<<1;
					moveStateX = 2;			//Start Phase 2
				}
				_flag=true;

			}
			else {
				// Otherwise, check velocity.
				if(labs(VelRefQx) >= VelLimitQx) {
					// If maximum velocity reached, compute TX1 and set AX = 0, and VelRefQx=VelLimitQx.
					if(_TX1 == 0) {
						AccelRefQx = 0;
						_TX1 = _TX;
						if(VelRefQx > 0)
							VelRefQx=VelLimitQx;
						else
							VelRefQx=-VelLimitQx;
					}
				}
			}
			break;

		case 2:		//Phase 2 2nd half of move
			// Execute move
			MovePosnQx = MovePosnQx + VelRefQx + (AccelRefQx>>1);
			VelRefQx = VelRefQx + AccelRefQx;

			// Check time.
			if(_TX >= _TX3) {
				// If beyond TX3, wait for done condition.
				AccelRefQx = -AccelRefQxS;
				if((_TX > _TAUX) || (labs(MovePosnQx) > labs(TargetPosnQx)) || (VelRefQx*AccelRefQx > 0)) {
            	// If done, enforce final position.
					AccelRefQx = 0;
					VelRefQx = 0;
					MovePosnQx = TargetPosnQx;
					moveStateX = 3;
					CommandX=0;
				}
			}
			break;
		case 4:		//Fast move case
			// Execute move
			TargetPosnQx = CommandX<<fractionalBits;
				MovePosnQx = TargetPosnQx;
			if(TargetPosnQx-MovePosnQx>50<<fractionalBits){
				MovePosnQx=MovePosnQx+50<<fractionalBits;
			}
			else{
				MovePosnQx = TargetPosnQx;
				CommandX=0;
				moveStateX = 3;
			}

			break;
		case 5:		//Continuous / Velocity move
			// Execute move
			TargetPosnQx = CommandX<<fractionalBits;
			MovePosnQx = TargetPosnQx;

			// Execute move
			//accelerate up to desired velocity
			MovePosnQx = MovePosnQx + VelRefQx + (AccelRefQx>>1);
			VelRefQx = VelRefQx + AccelRefQx;

			if(labs(VelRefQx) >= VelLimitQx) {
			  // If maximum velocity reached, compute TX1 and set AX = 0, and VelRefQx=VelLimitQx.
			    if(_TX1 == 0) {
			      AccelRefQx = 0;
			      _TX1 = _TX;
			      //Set velocity
			      if(VelRefQx > 0)
				VelRefQx=VelLimitQx;
			      else
				VelRefQx=-VelLimitQx;
			    }
			  }
			// if(TargetPosnQx-MovePosnQx>50<<fractionalBits){
			//   MovePosnQx=MovePosnQx+50<<fractionalBits;
			// }
			// else{
			//   MovePosnQx = TargetPosnQx;
			//   CommandX=0;
			//   moveStateX = 3;
			// }

			break;
	}
	// Compute burst value
	_BurstX = (MovePosnQx - StepsSent)>>fractionalBits;
	// Update accumulated integer position
	StepsSent += (long)(_BurstX)<<fractionalBits;

	//check which direction, and incement absPosition
	if(_direction)
		AbsPosition+=_BurstX;
	else
		AbsPosition-=_BurstX;
	return _BurstX;

}


/*
	This is the default constructor.  This intializes the variables.
*/
ClearPathMotorSD::ClearPathMotorSD()
{
	moveStateX=3;
	PinA=0;
	PinB=0;
	PinE=0;
	PinH=0;
	Enabled=false;
	VelLimitQx=0;
	AccLimitQx=0;
	MovePosnQx=0;
	StepsSent=0;
	VelRefQx=0;
	AccelRefQx=0;
	_TX=0;
	_TX1=0;
	_TX2=0;
	_TX3=0;
	_TAUX=0;
	_flag=0;
	AccelRefQxS=0;
	TargetPosnQx=0;
	TriangleMovePeakQx=0;
	CommandX=0;
	fractionalBits=10;
	_BurstX=0;
	AbsPosition=0;
}

/*
	This is the one pin attach function.  It asociates the passed number, as this motors Step Pin
*/
void ClearPathMotorSD::attach(int BPin)
{
  PinA=0;
  PinB=BPin;
  PinE=0;
  PinH=0;
  pinMode(PinB,OUTPUT);
}
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

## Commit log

2020-10-27 added pcb files
    [dbt-mini-shield.brd, dbt-mini-shield.sch]
2020-10-27 pcb files
    [dbt_shield_v2_v23.sch, dbt_shield_v2_v30.brd]
2020-10-27 new pcb eagle 9 compatible file
    [dbt-mini-shield.brd]

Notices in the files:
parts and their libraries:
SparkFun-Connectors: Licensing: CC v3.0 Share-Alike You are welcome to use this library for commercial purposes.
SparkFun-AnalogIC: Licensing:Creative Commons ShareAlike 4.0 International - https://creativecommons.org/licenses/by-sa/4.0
